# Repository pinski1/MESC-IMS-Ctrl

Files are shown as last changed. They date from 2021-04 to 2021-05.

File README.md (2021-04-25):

# MESC IMS Ctrl
A derivative of the Molony ESC. STM32F303 based BLDC logic board designed to interface to an IMS power stage.

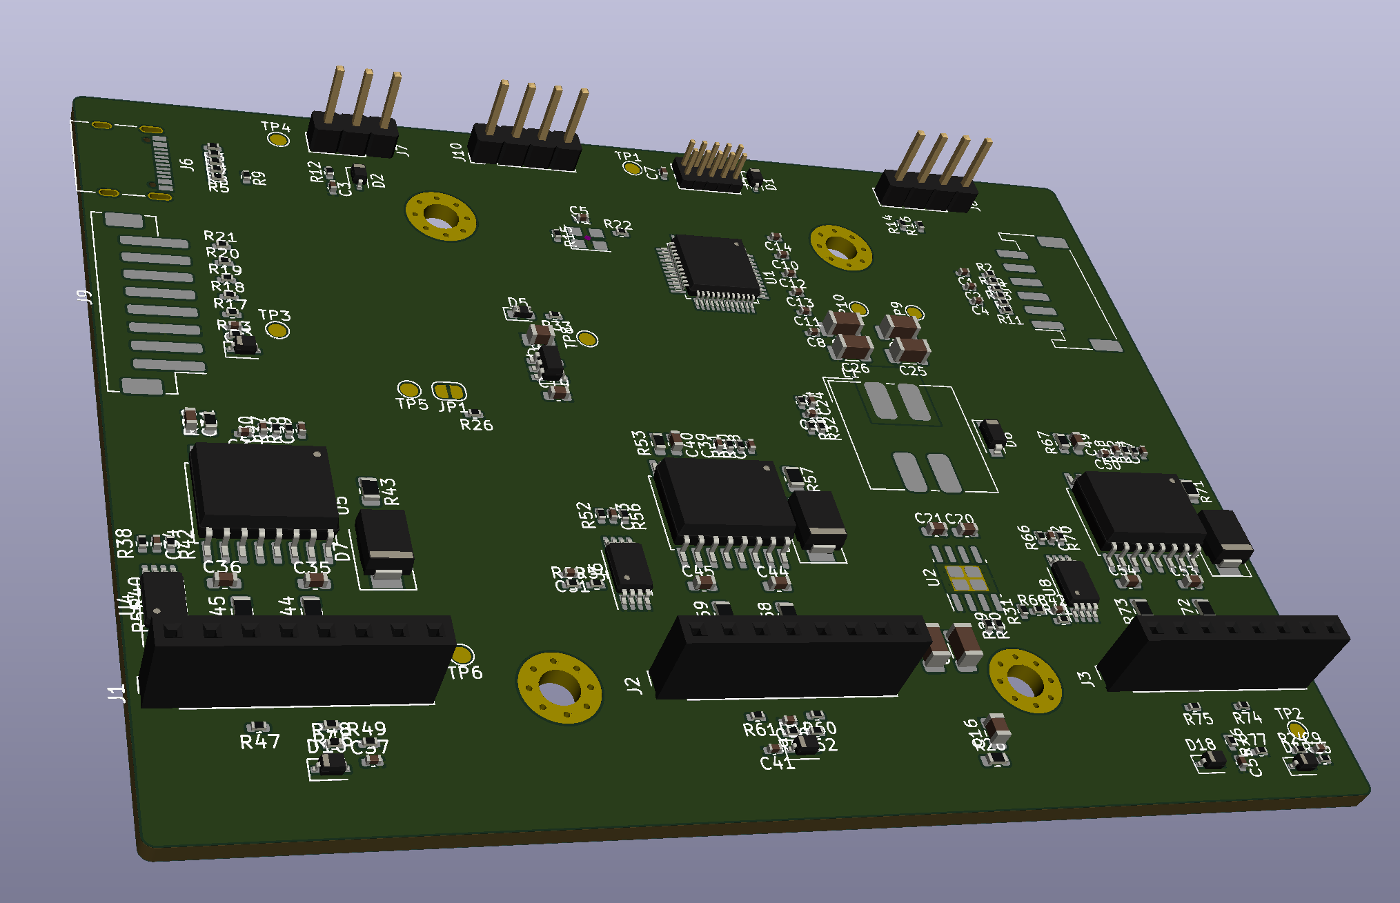
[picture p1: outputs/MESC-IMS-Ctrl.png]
An initial 3D render of the board.


Please see https://github.com/davidmolony/MESC_FOC_ESC for further details.

For the most recent schematic check out the 'outputs' folder.

This board is designed to fit on a 12FET power stage IMS PCB
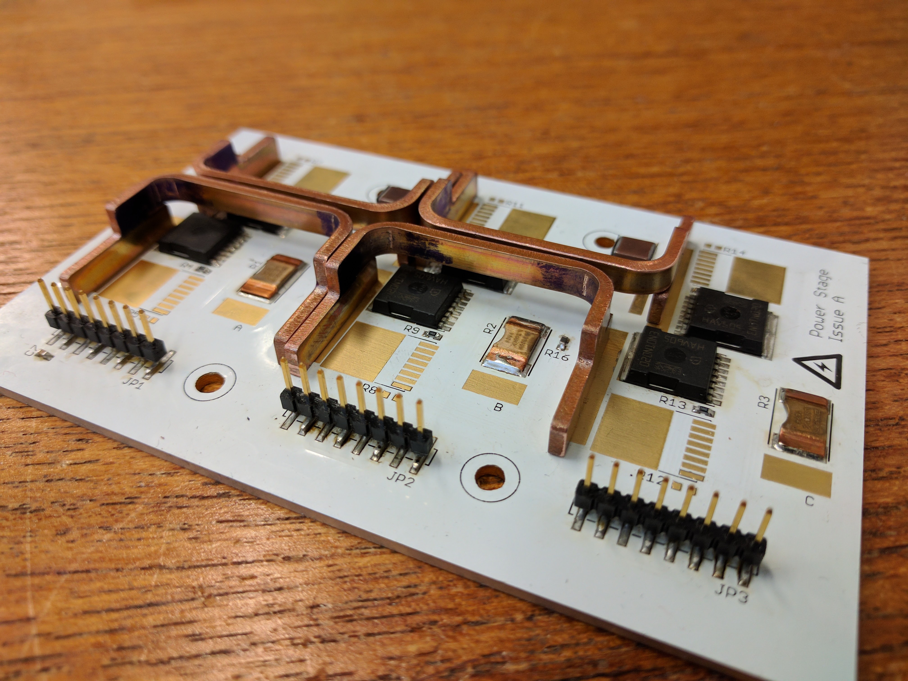
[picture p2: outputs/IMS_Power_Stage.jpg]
The 12FET Power stage with only half the MOSFETs


## "MESC_IMS_Ctrl.sch"

* Using STM32F303 like MESC_FOC_ESC
* Using USB 2.0 type C connector for future compatibility
* Using VESC-style connectors for control & hall effect sensors
* Has facility to monitor a thermistor mounted to the power stage PCB
* Can monitor the battery voltage
* Can be powered via USB for configuration on the desk

## "psu.sch"
This sheet contains the power supplies for the ESC. It's designed to accept +40-50V input but won't activate at voltages less than +25V. The LM5-017 is a popular and robust SMPS buck convertor. To minimise supply rail noise but supply the requisite ripple for the feedback circuitry the Texas Instruments application note here: https://www.ti.com/lit/an/snva166a/snva166a.pdf was consulted.

By using a coupled inductor it is possible to get a 2nd, unregulated, output that can be 'stacked' on top of the regulated output. This provides a ~10V supply for the gate drivers. This method of using a coupled inductor to generate a 2nd output is detailed in this Texas Instruments application note here: https://www.ti.com/lit/pdf/snva674.

The +3V3 rail for the microcontroller and current amplifiers comes from a standard SOT23-5 LDO. This minimises noise artefacts and is a simple, low cost, low complexity way of generating this rail.

## "phase.sch"
As this board will plug into the separate power stage PCB it was decided to use isolated gate driver chips. As the gate signals are treated as differential signals this should hopefully allow for fast control while minimising noise, minimising ripple and self-turn-on. The UCC21520 is another well regarded chip. 

The INA240 is used for high speed current sensing, it will take the differential phase current sense signals at the phase voltage and convert them to a single ended current signal with 0A being around 1.65V. There is no additional filtering as this will affect the response of the current amplifier.

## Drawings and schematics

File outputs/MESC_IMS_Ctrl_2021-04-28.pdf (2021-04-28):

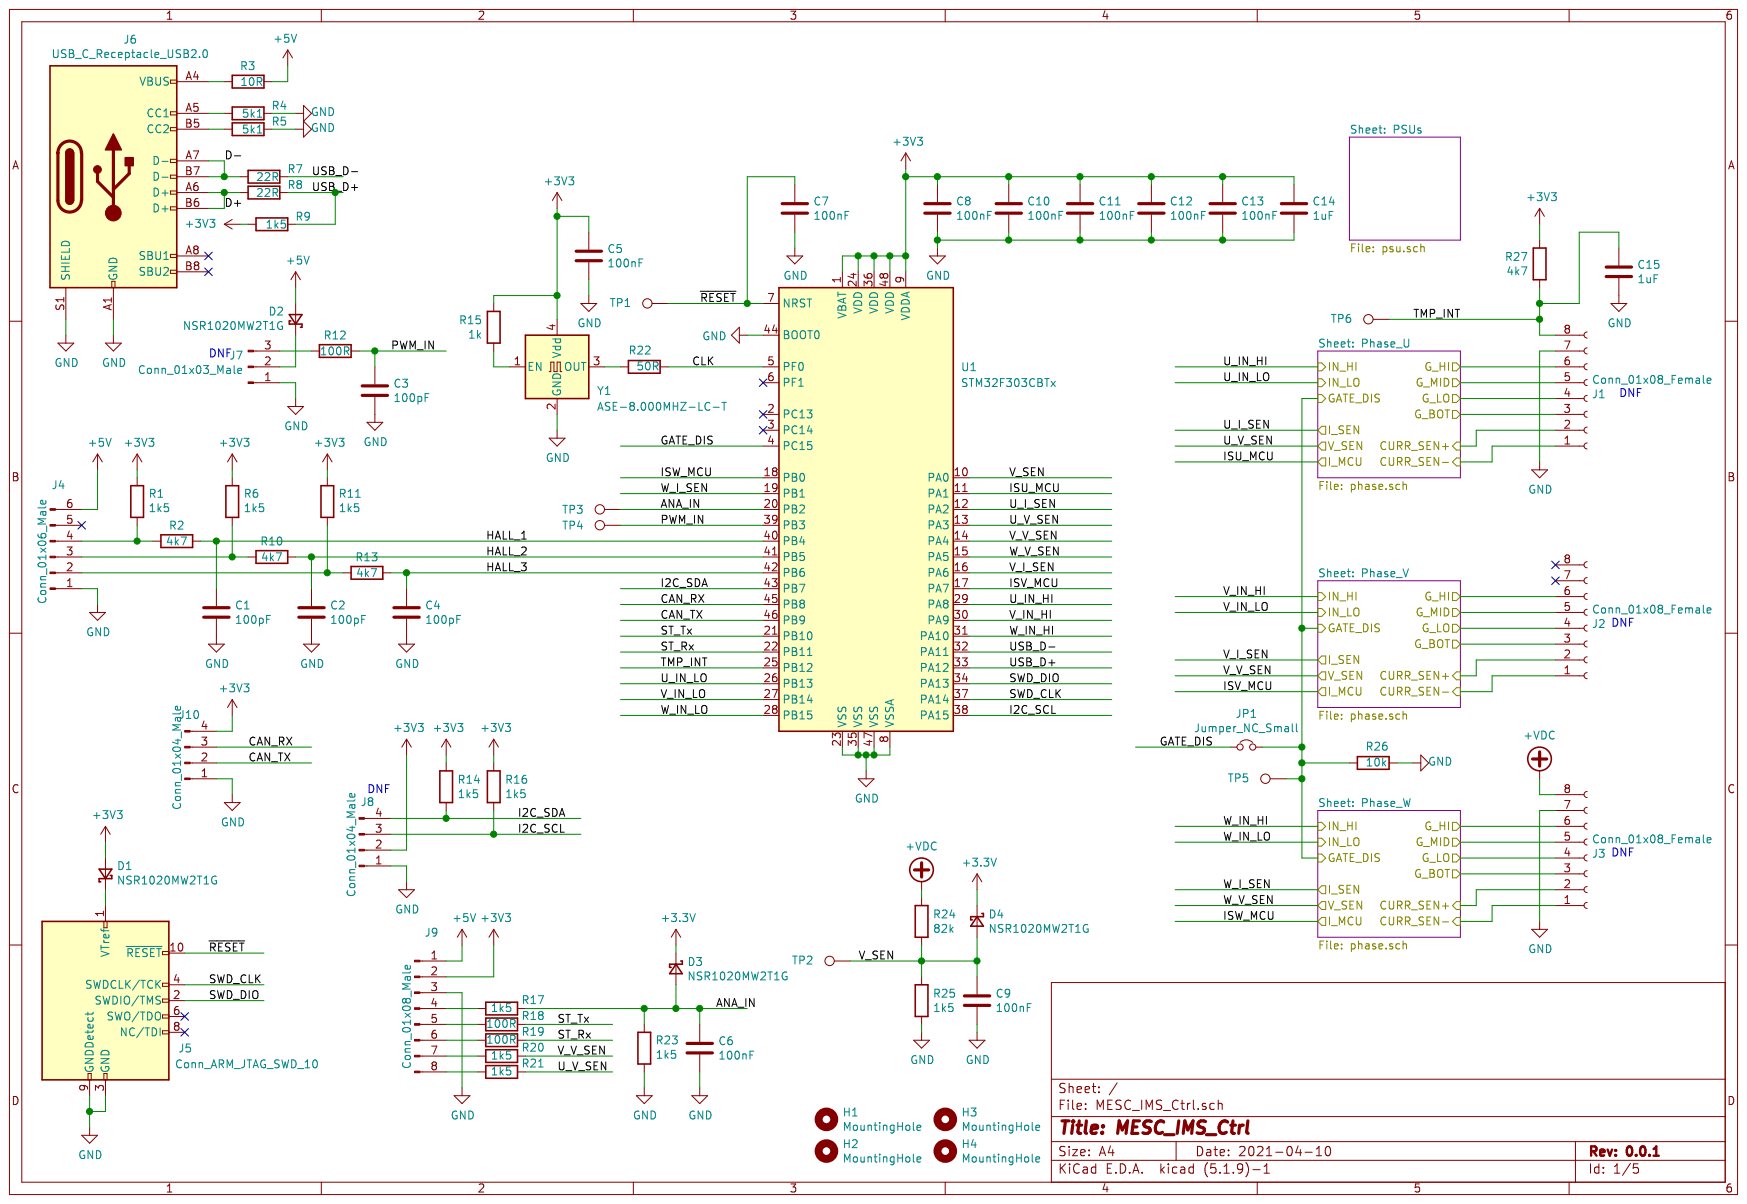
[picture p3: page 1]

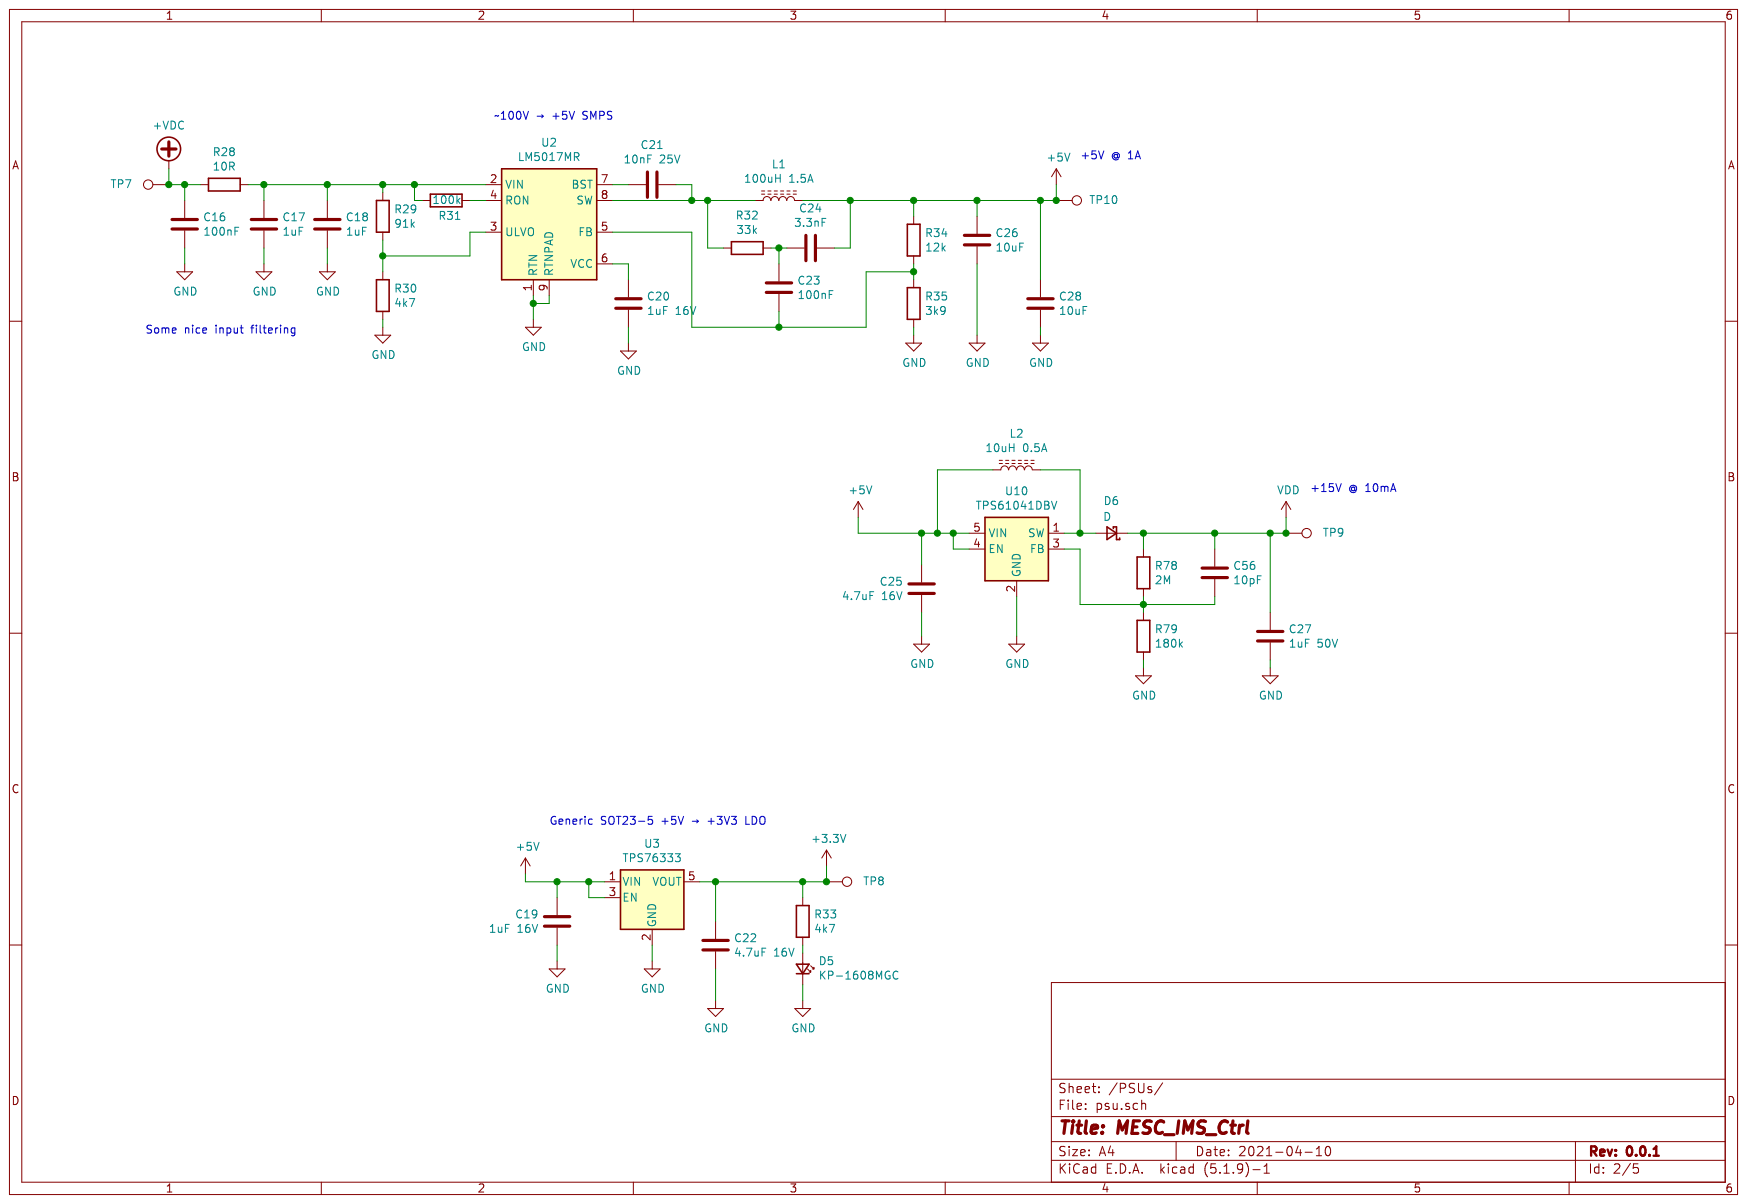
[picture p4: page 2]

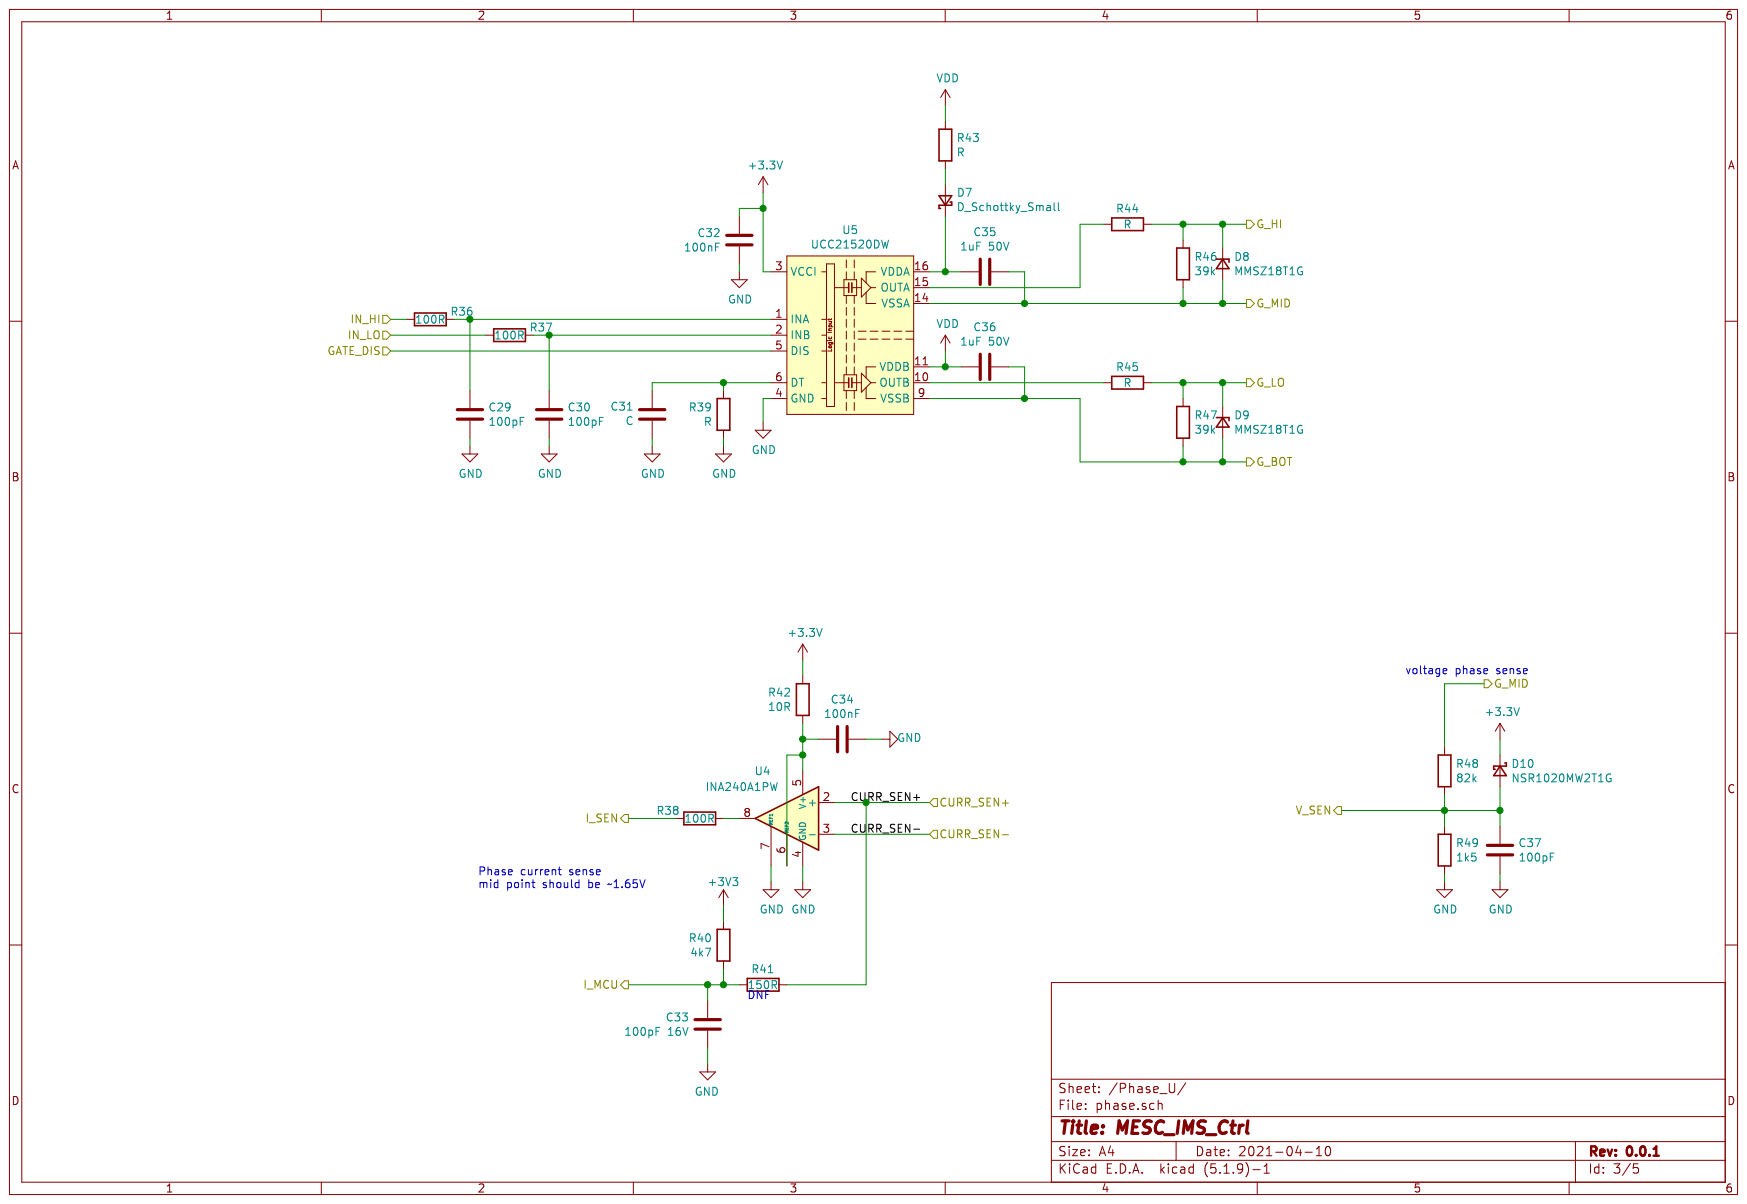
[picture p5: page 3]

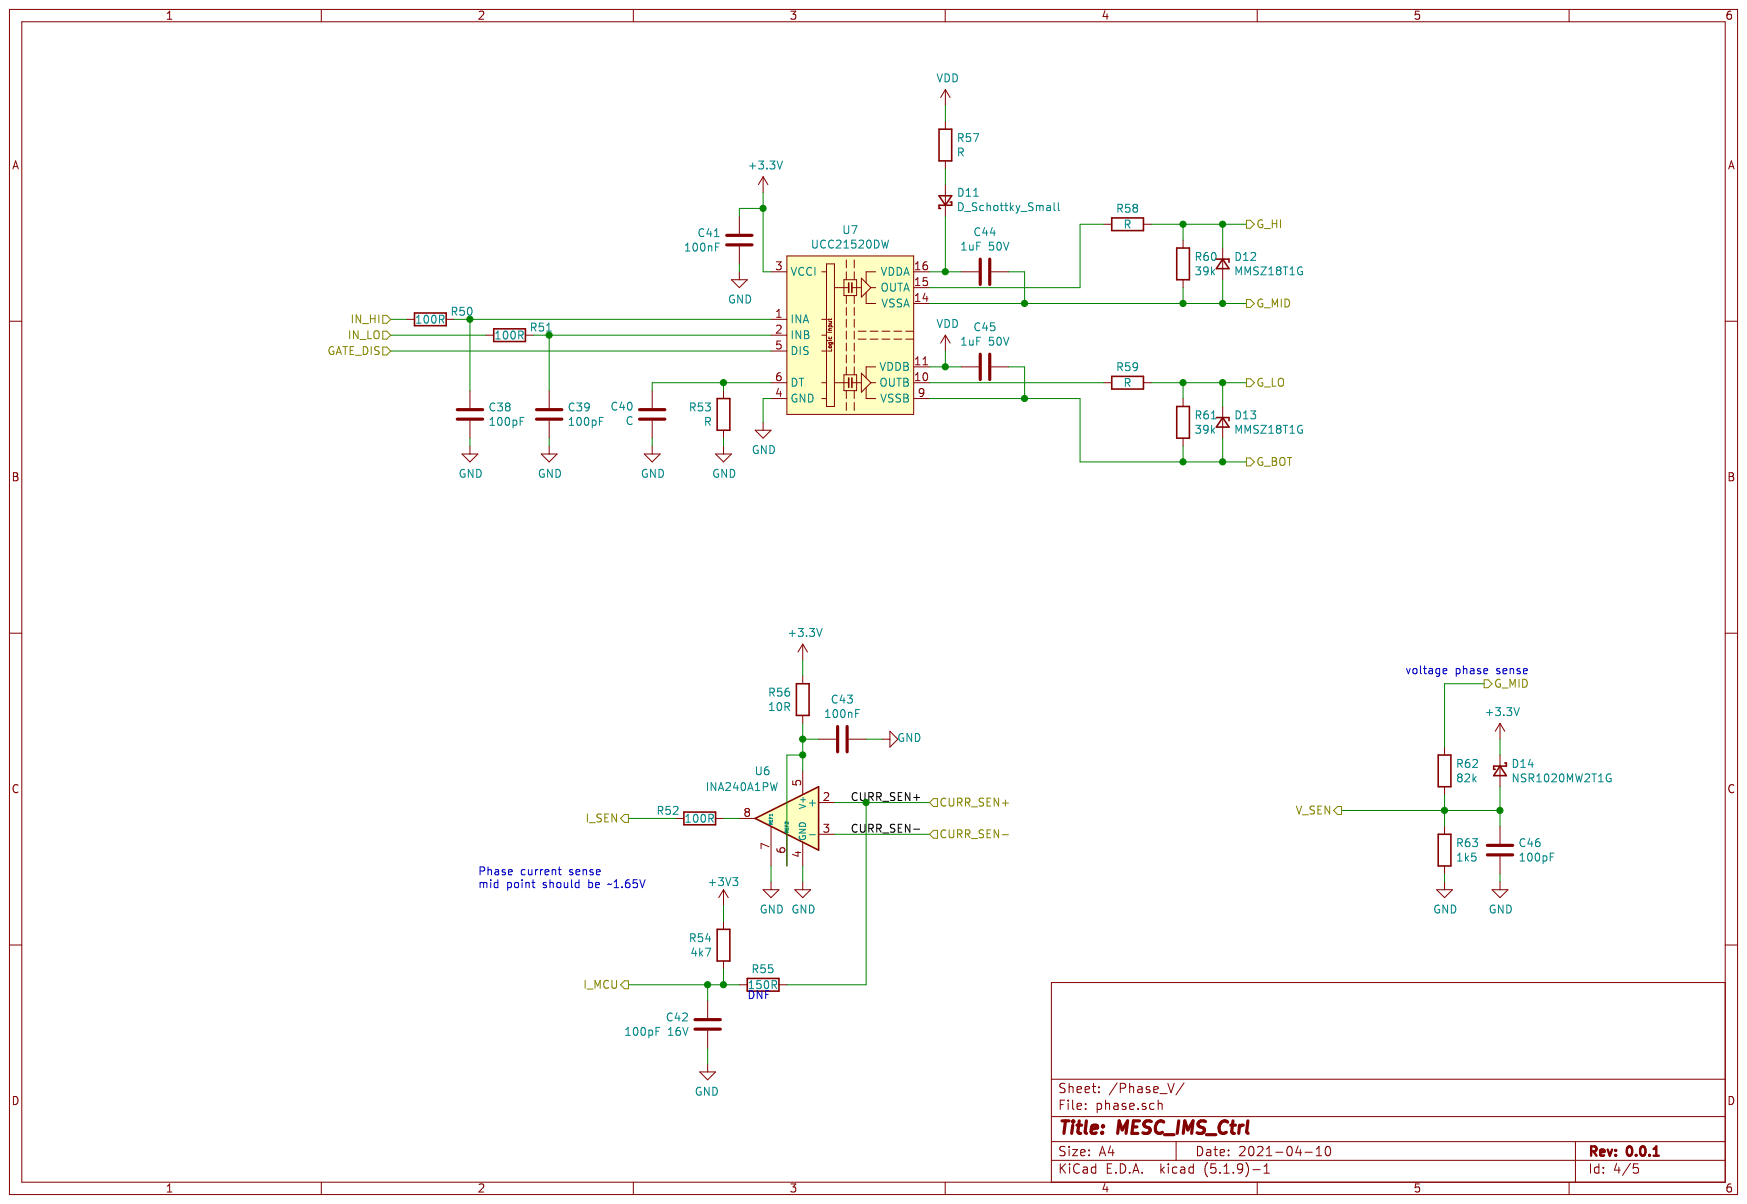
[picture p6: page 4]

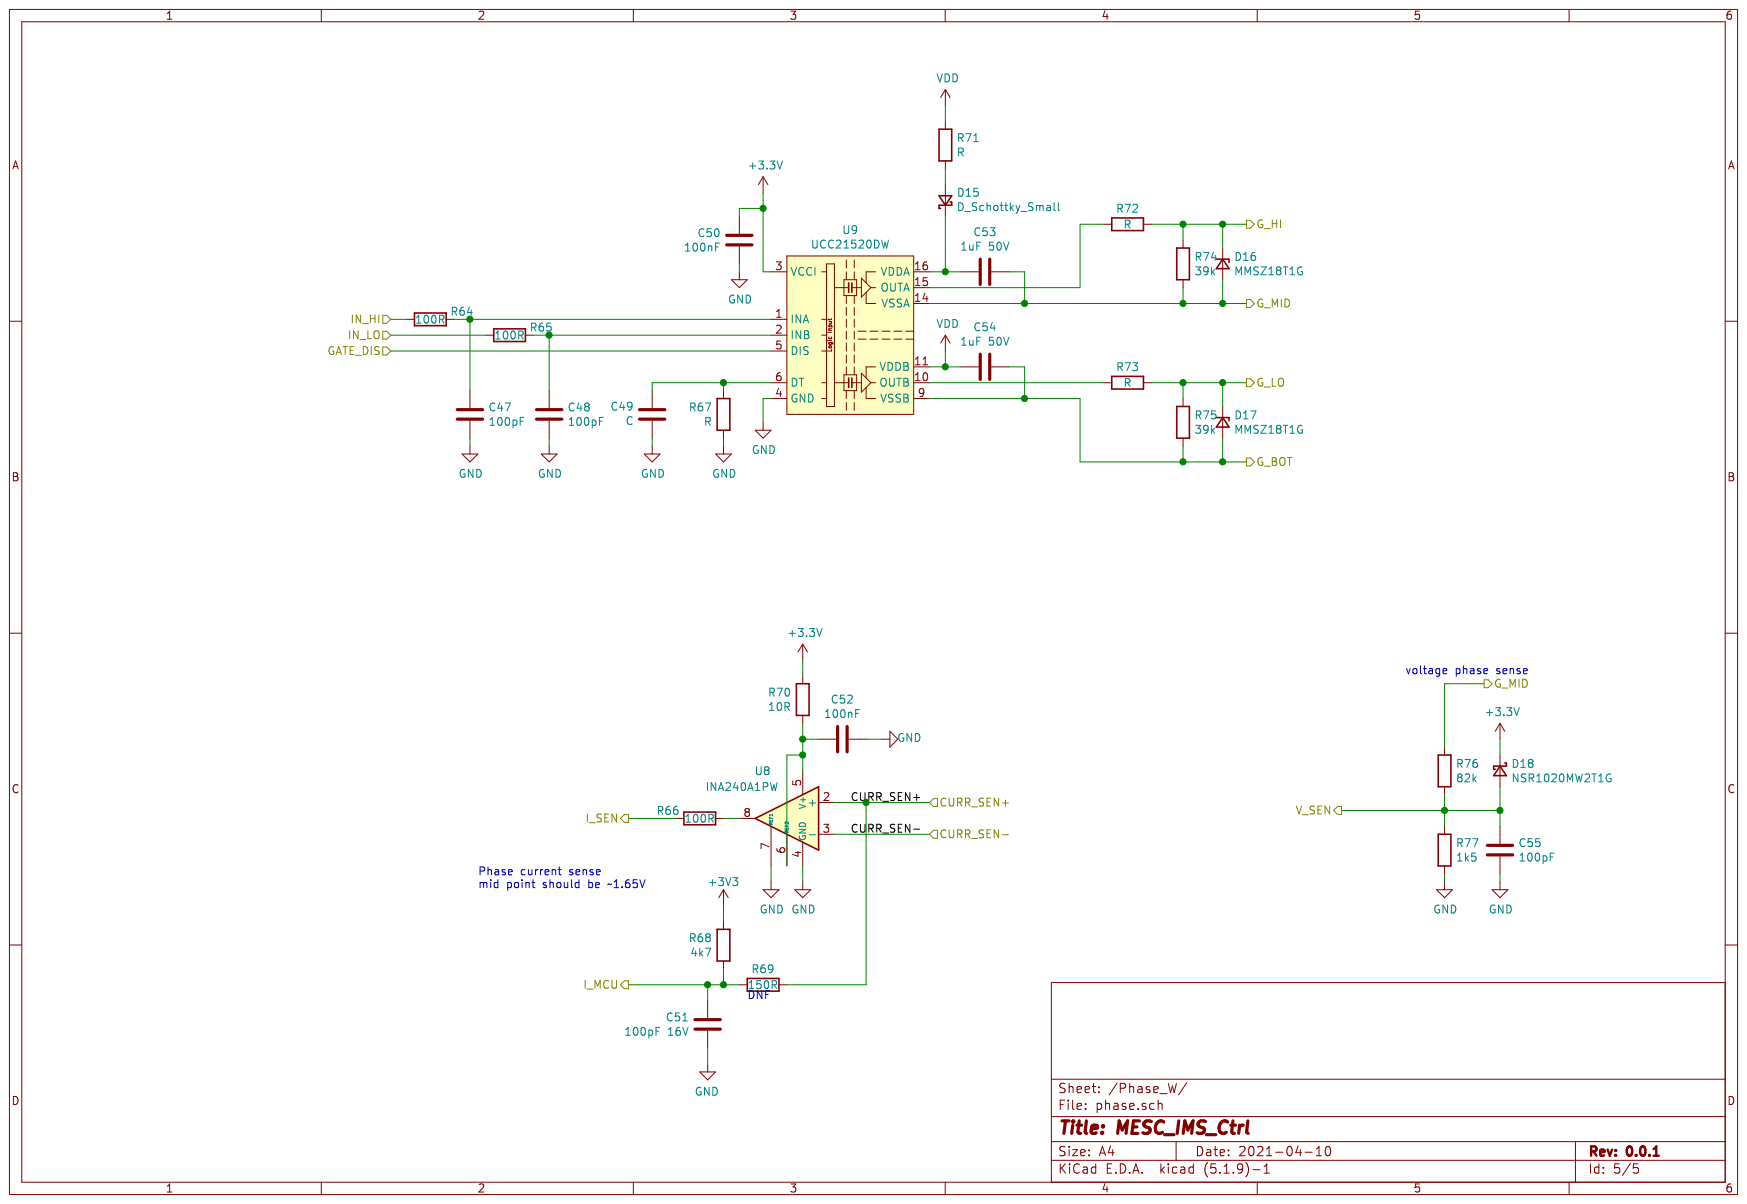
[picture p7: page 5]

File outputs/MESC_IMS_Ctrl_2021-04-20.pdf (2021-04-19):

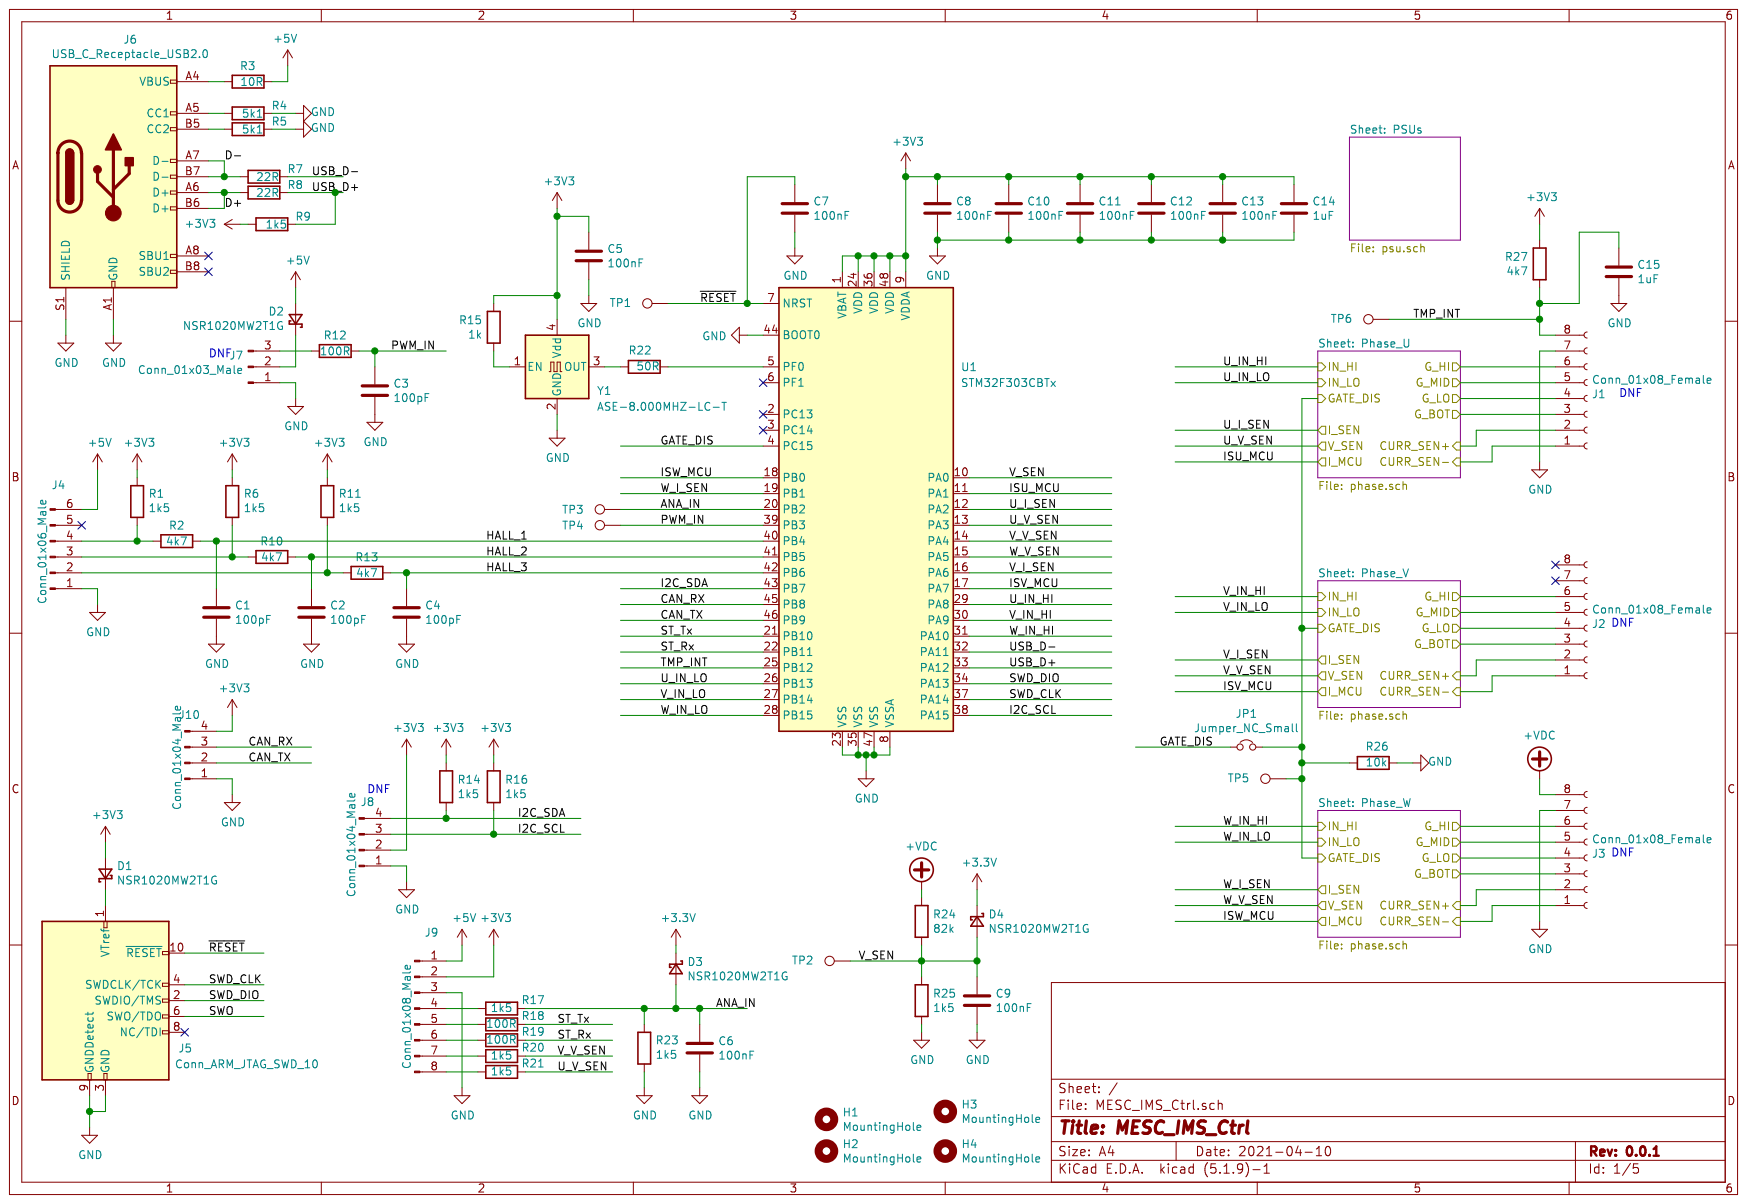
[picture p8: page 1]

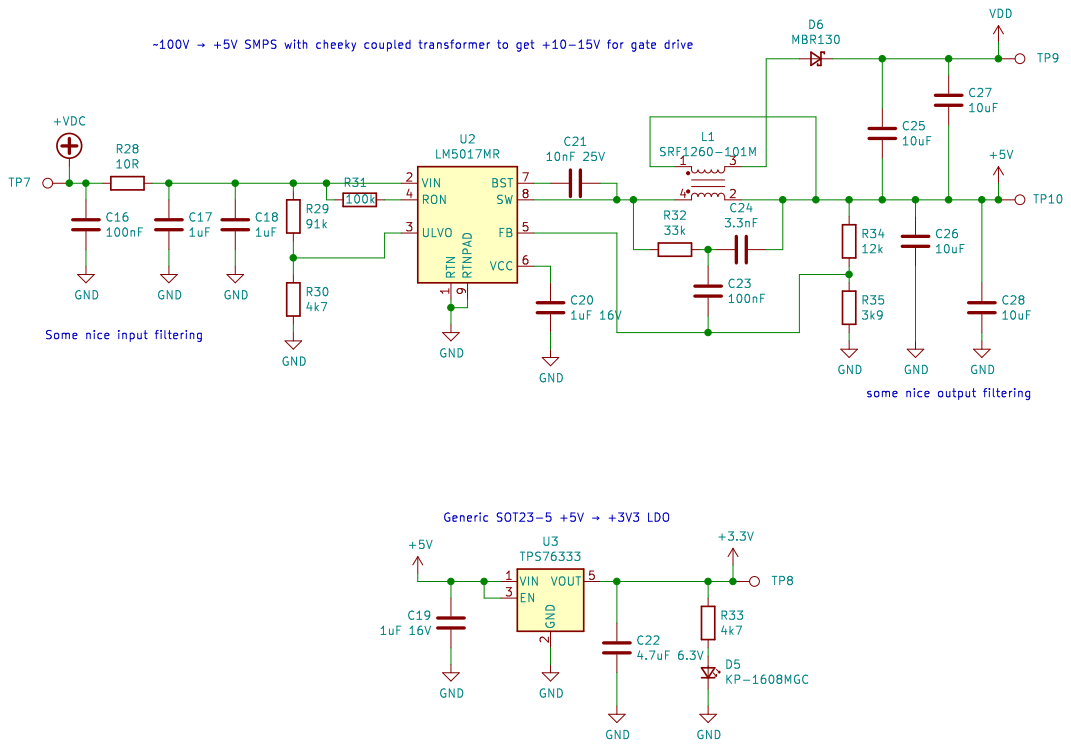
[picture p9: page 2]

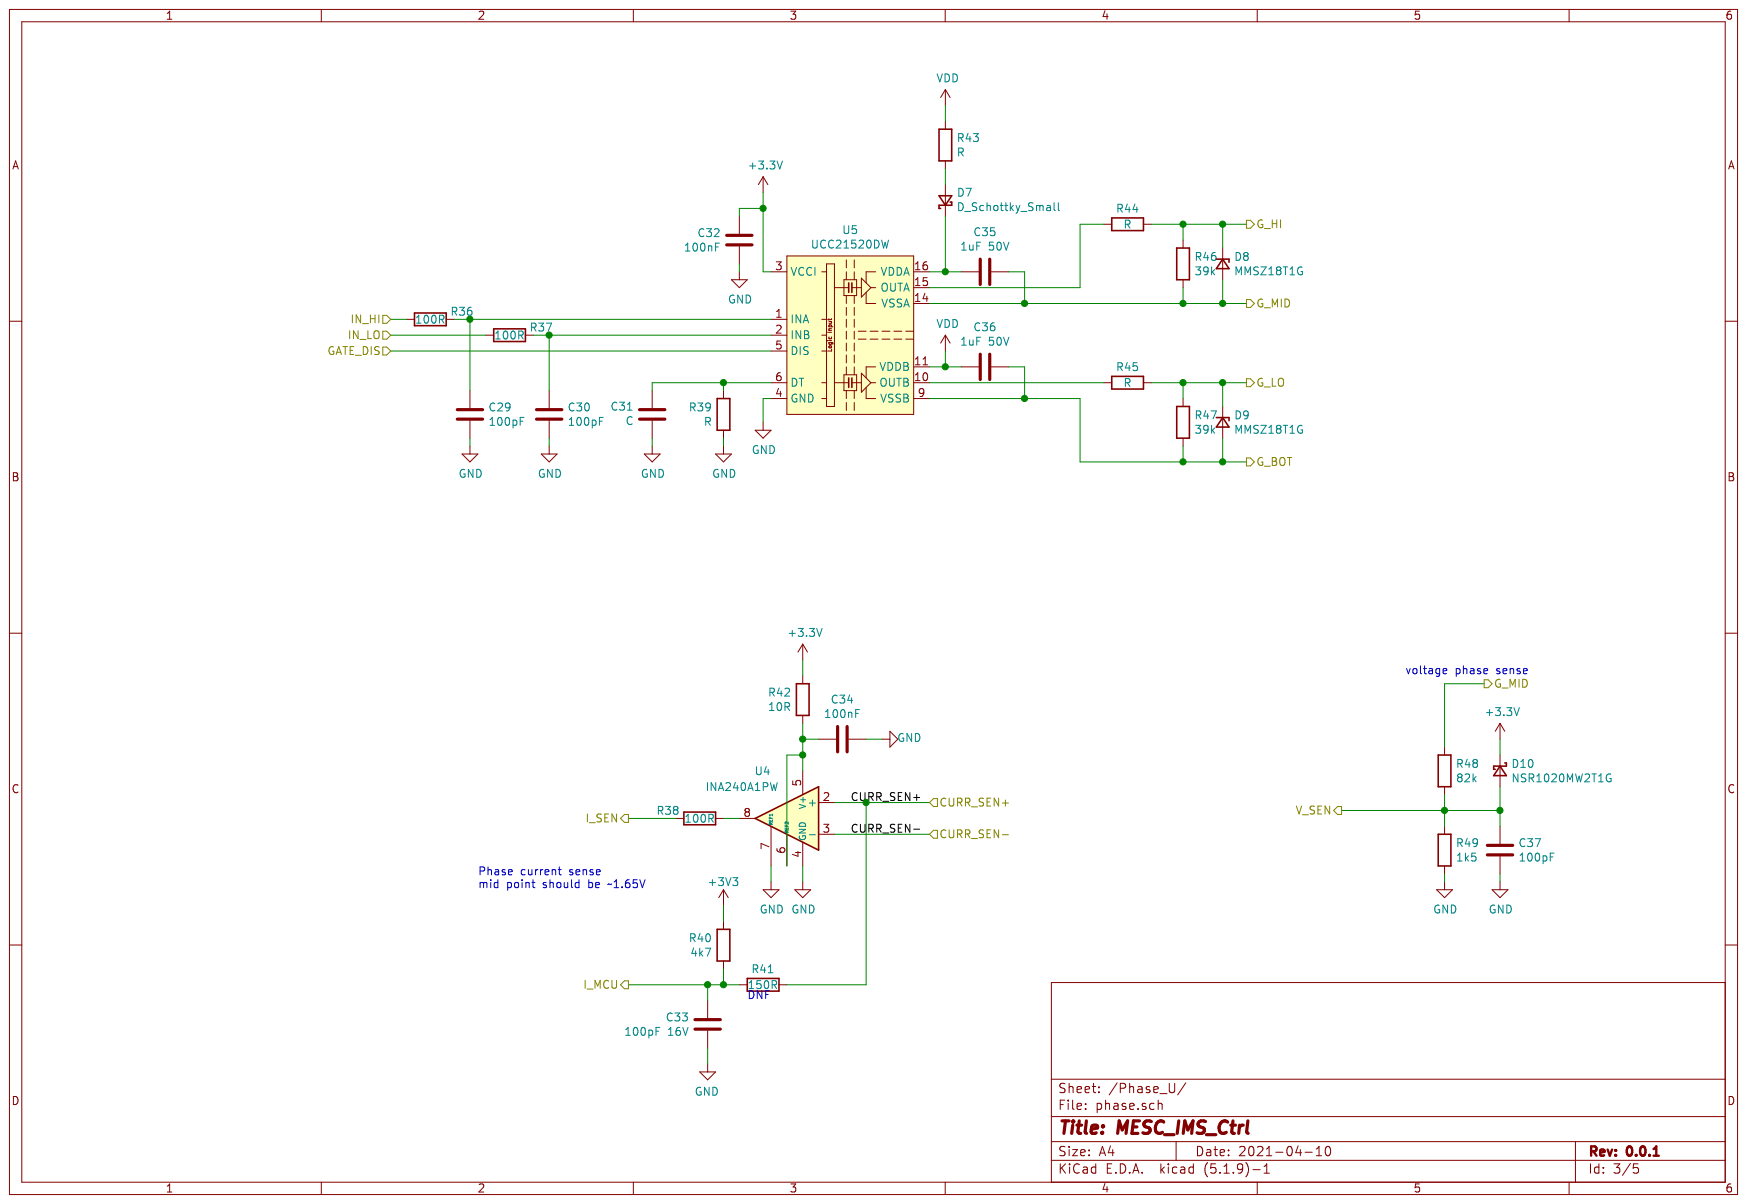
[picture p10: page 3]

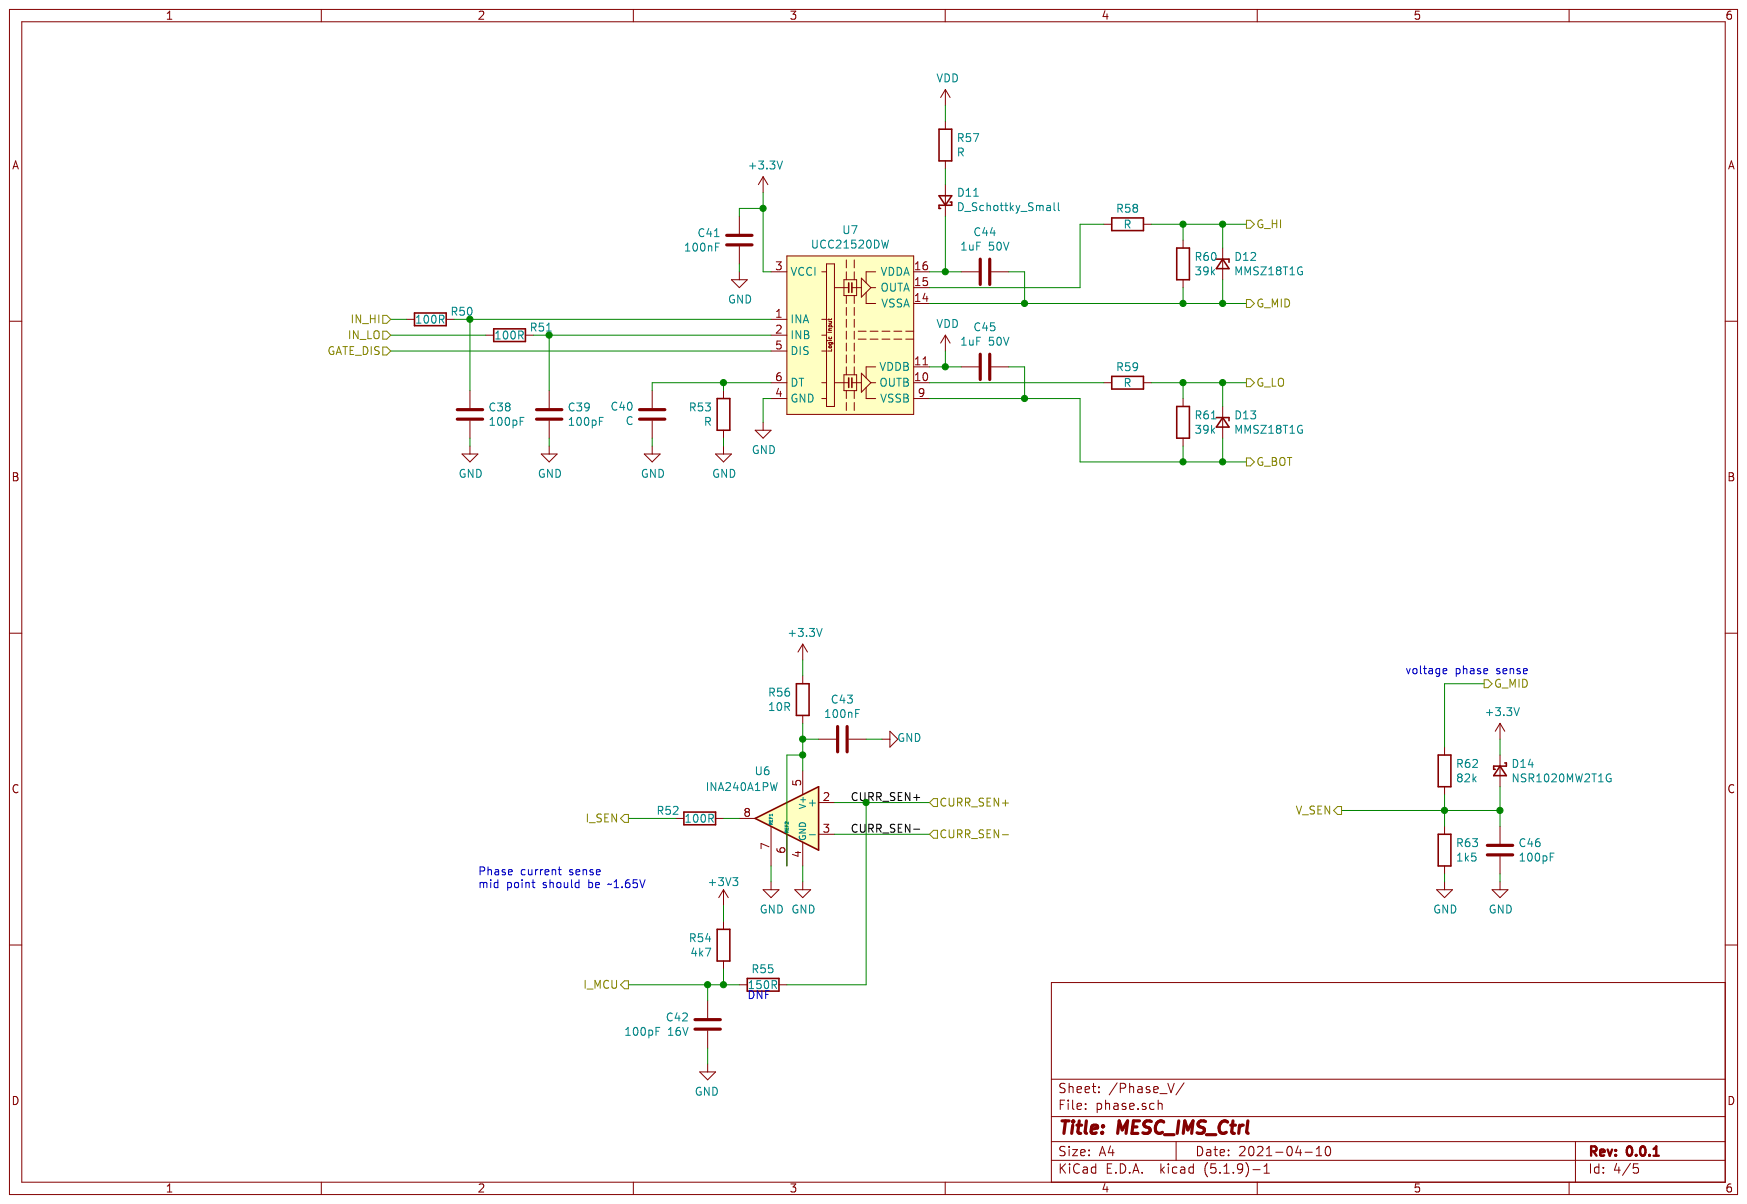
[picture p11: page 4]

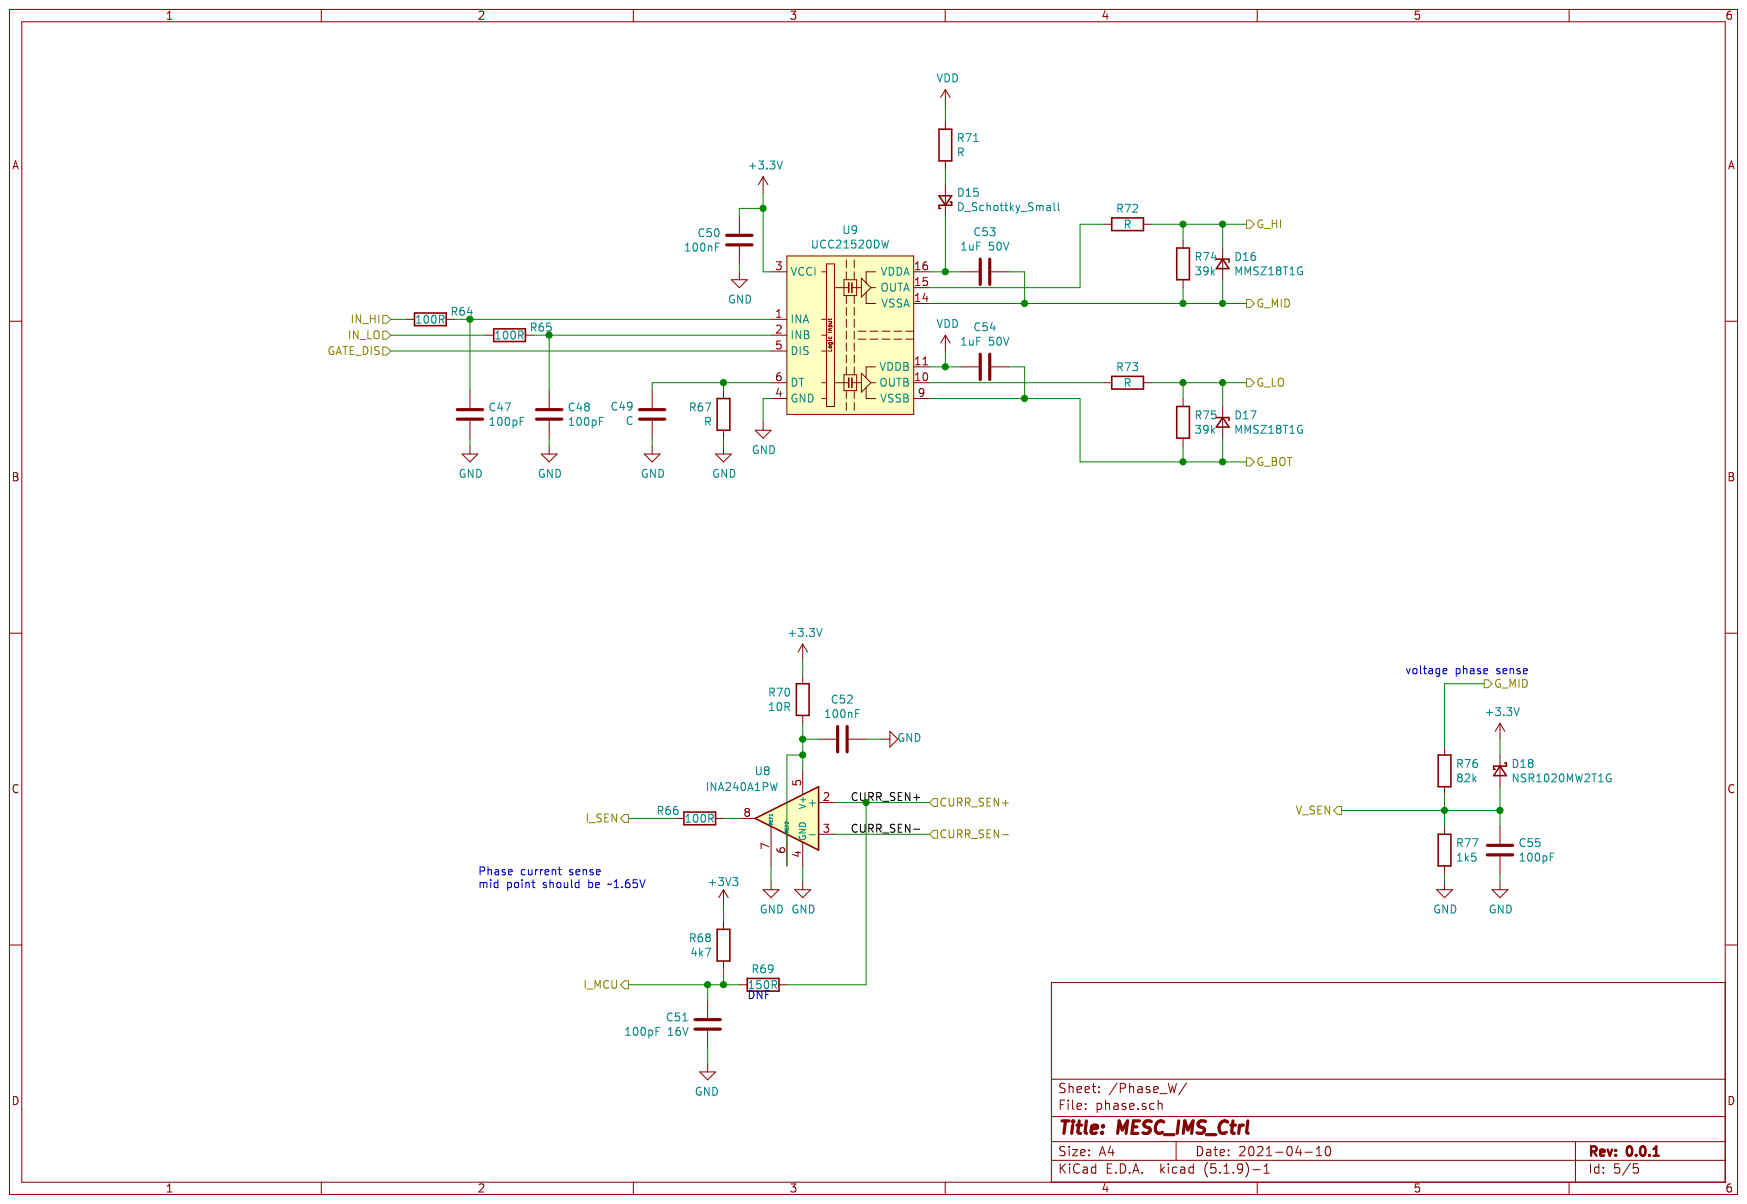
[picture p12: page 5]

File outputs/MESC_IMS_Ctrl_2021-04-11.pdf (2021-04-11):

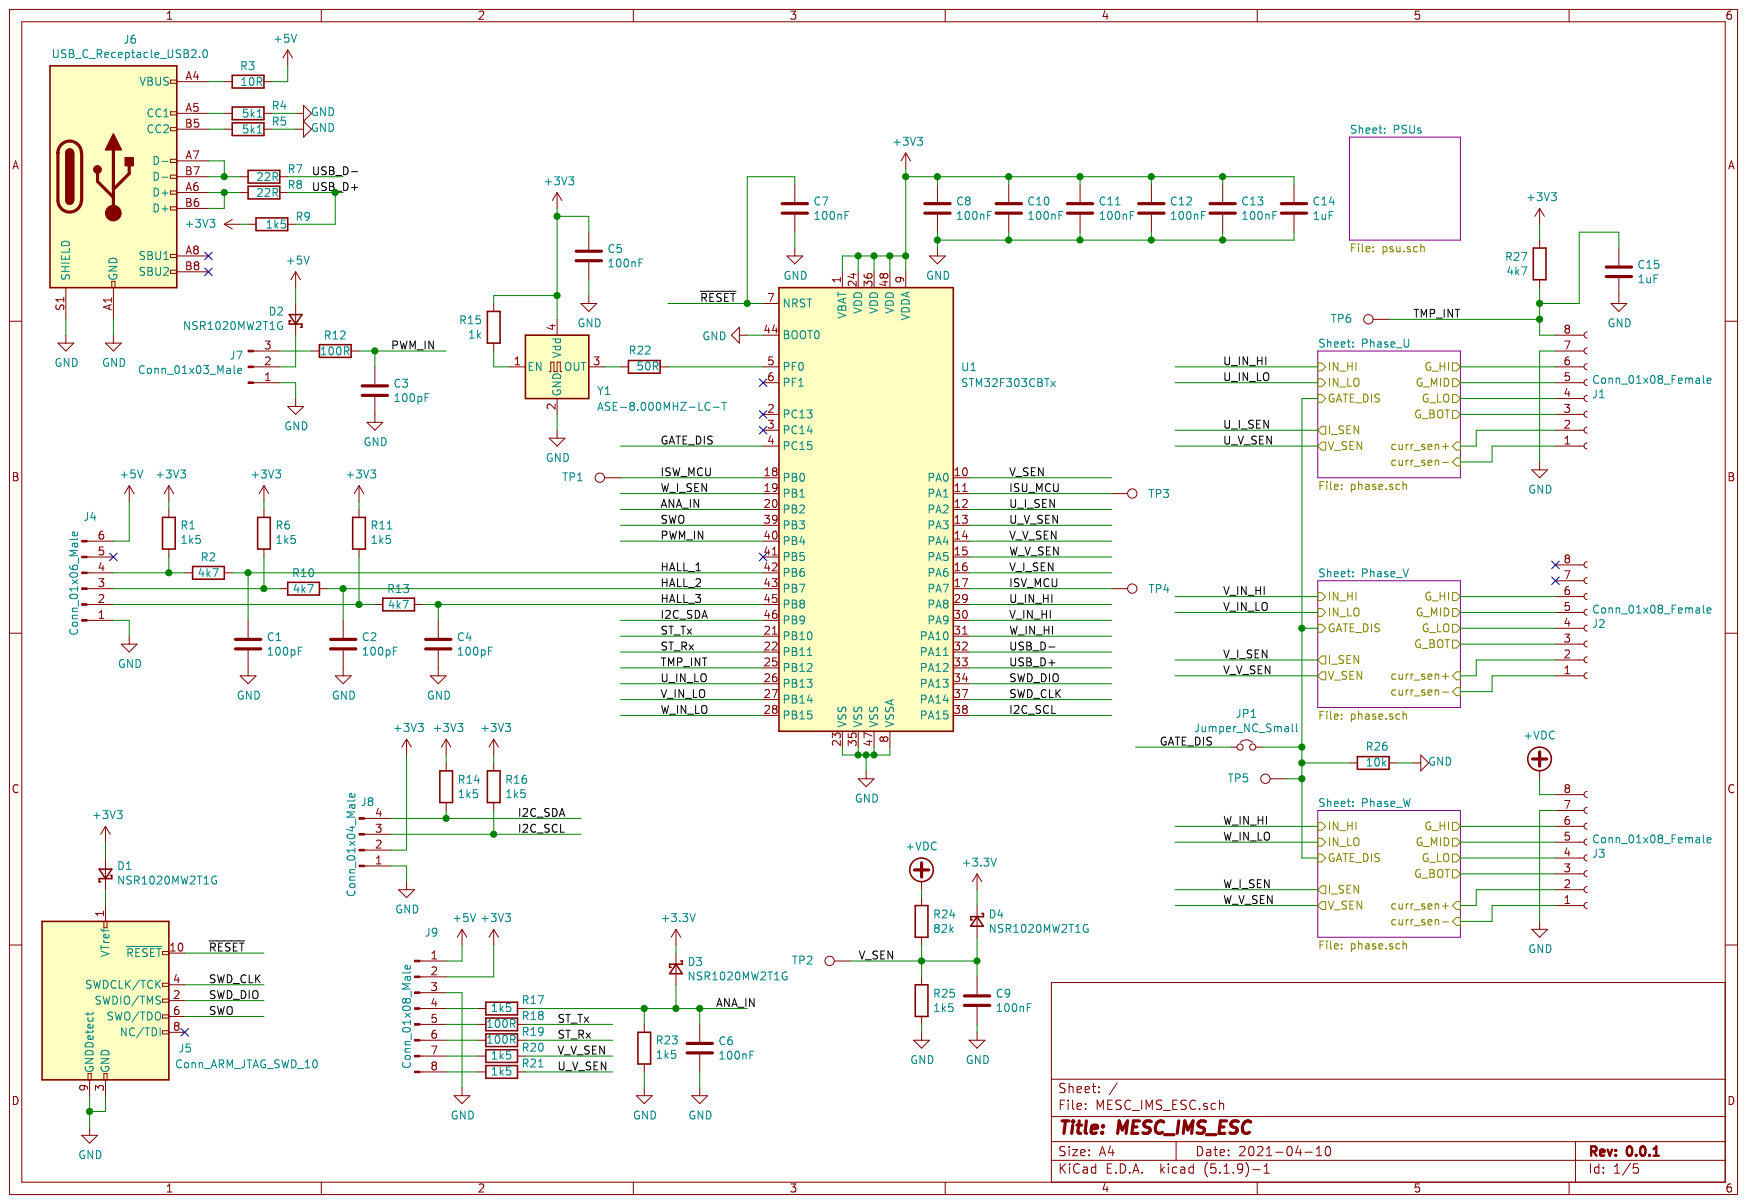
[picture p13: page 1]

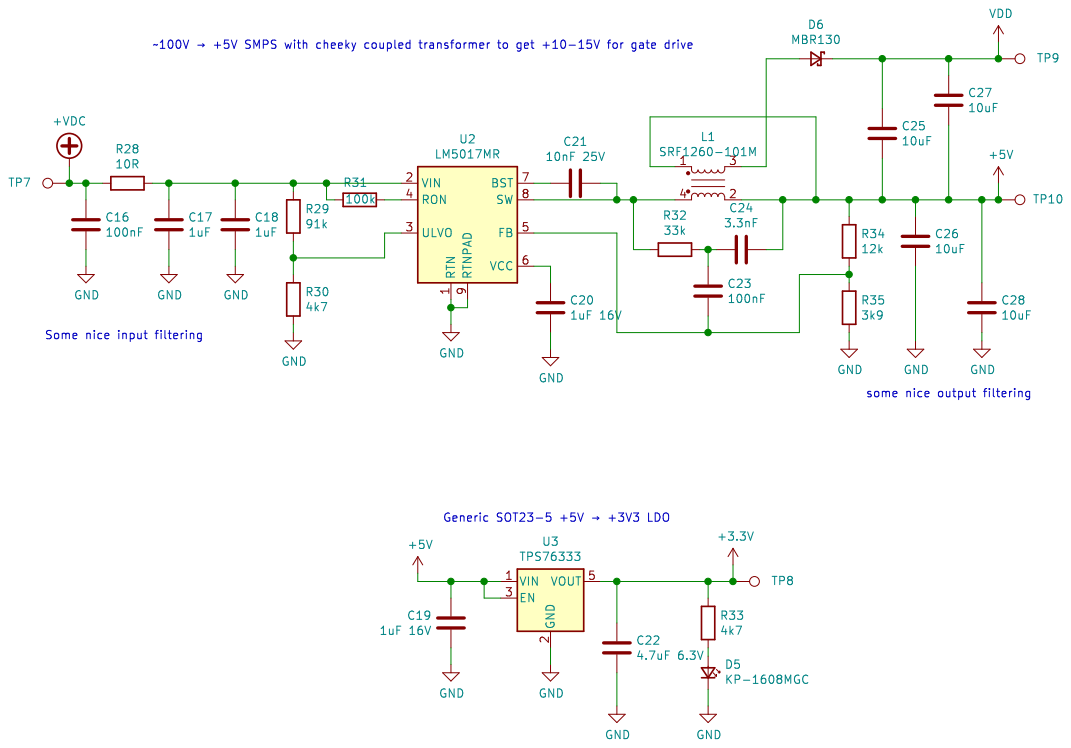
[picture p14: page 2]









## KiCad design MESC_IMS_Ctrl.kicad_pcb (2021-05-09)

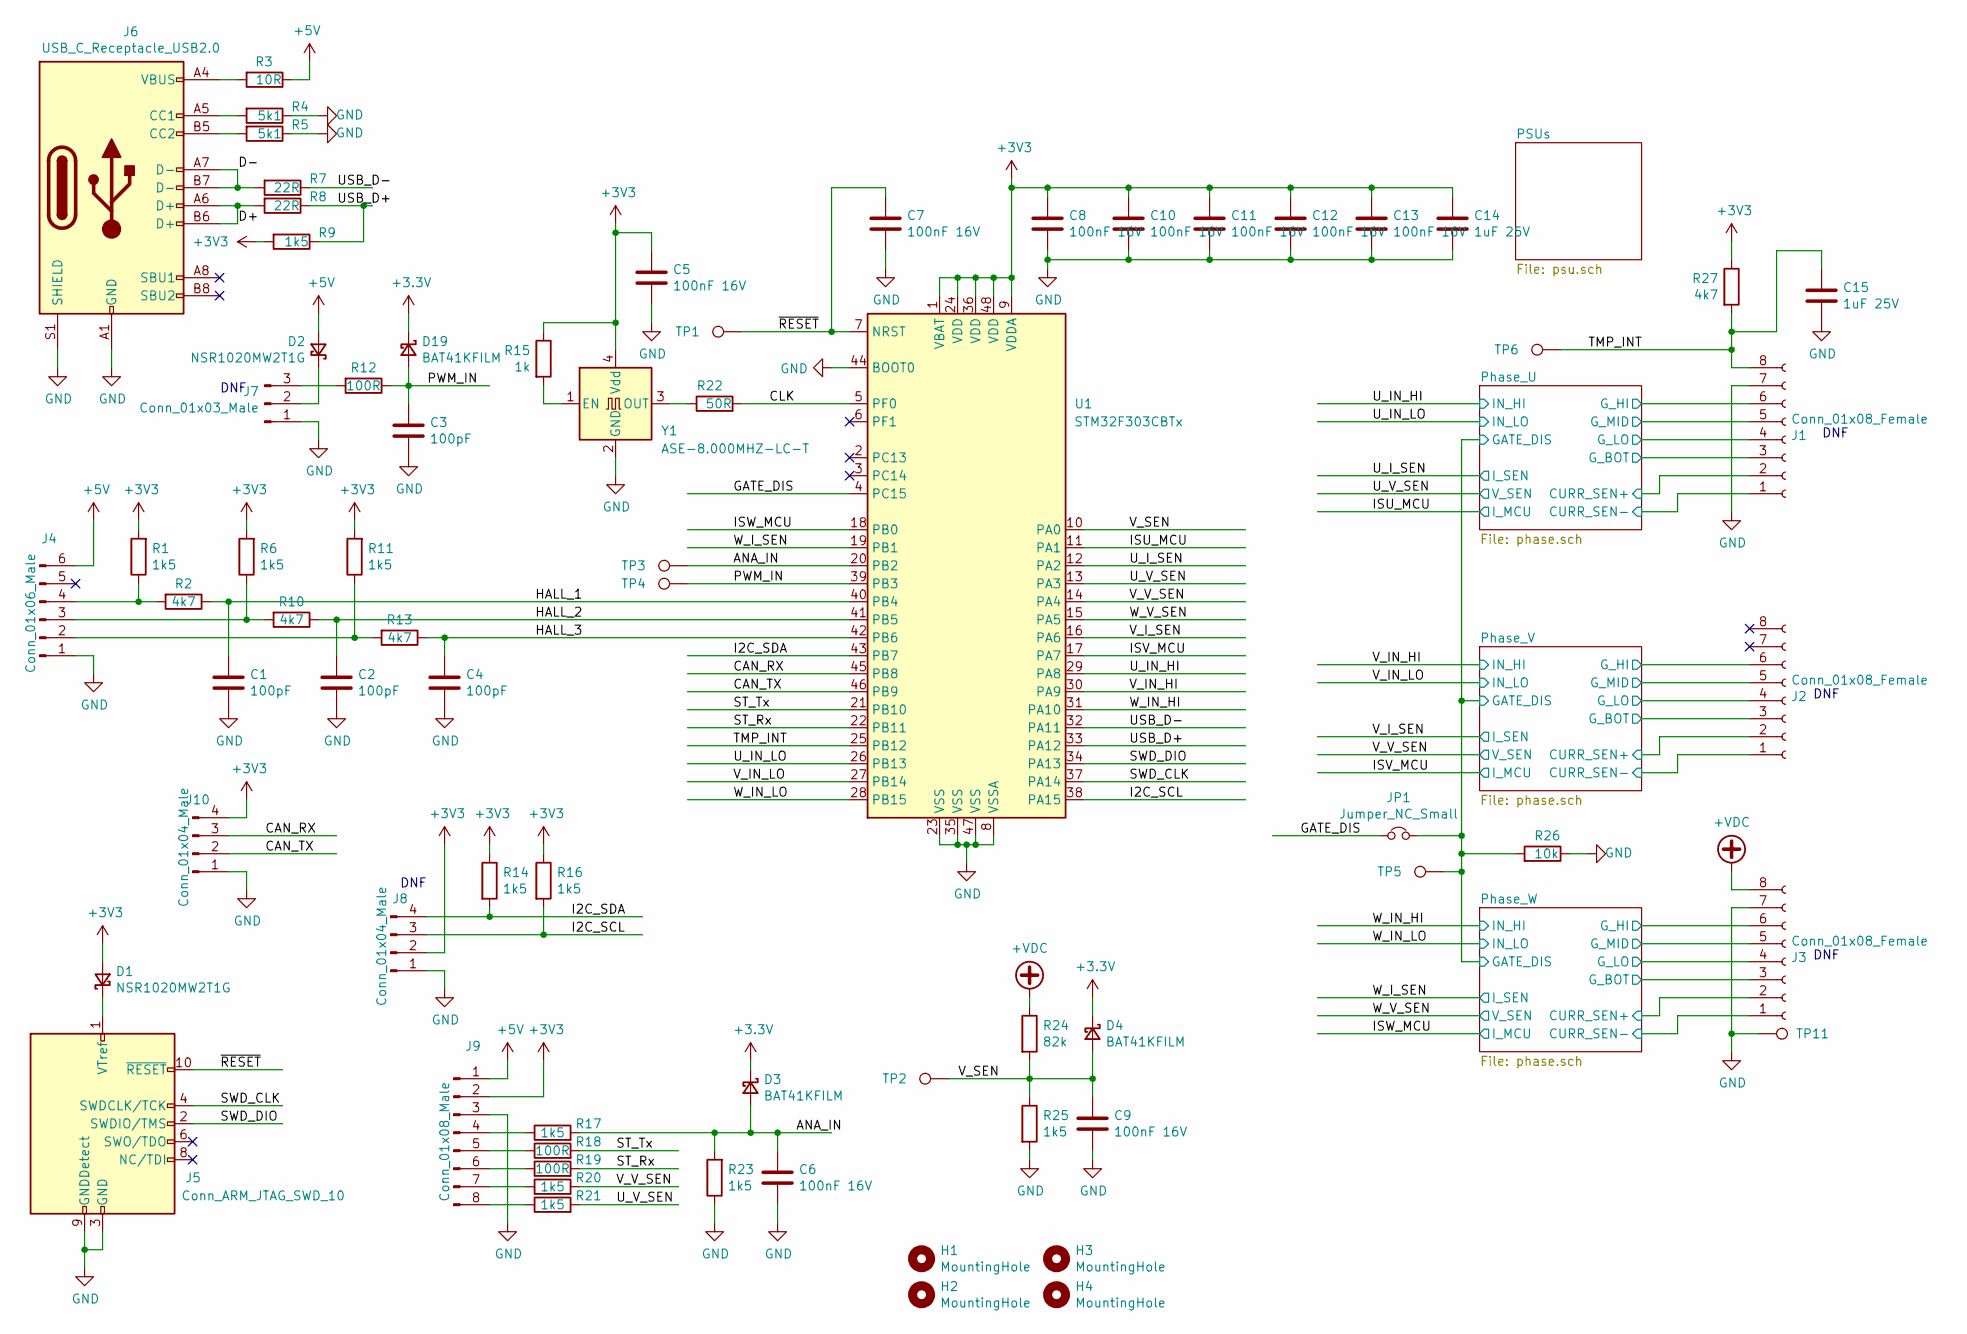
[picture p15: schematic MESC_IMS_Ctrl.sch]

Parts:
C1, C2, C3, C4: 100pF; C_0402_1005Metric; LCSC C1546
C5, C6, C7, C8, C9, C10, C11, C12, C13: 100nF 16V; C_0402_1005Metric; LCSC C1525
C14, C15: 1uF 25V; C_0402_1005Metric; LCSC C52923
D1, D2: NSR1020MW2T1G; D_SOD-323; LCSC C116953
D3, D4, D19: BAT41KFILM; D_SOD-523; LCSC C73150
H1, H2, H3, H4: MountingHole; MountingHole_3.2mm_M3_Pad_Via
J1, J2, J3: Conn_01x08_Female; PinSocket_1x08_P2.54mm_Vertical
J4: Conn_01x06_Male; JST_PH_S6B-PH-SM4-TB_1x06-1MP_P2.00mm_Horizontal; LCSC C225237
J5: Conn_ARM_JTAG_SWD_10; PinHeader_2x05_P1.27mm_Vertical; LCSC C239059
J6: USB_C_Receptacle_USB2.0; USB_C_Receptacle_Palconn_UTC16-G; LCSC C165948
J7: Conn_01x03_Male; PinHeader_1x03_P2.54mm_Vertical
J8, J10: Conn_01x04_Male; PinHeader_1x04_P2.54mm_Vertical
J9: Conn_01x08_Male; JST_PH_S8B-PH-SM4-TB_1x08-1MP_P2.00mm_Horizontal; LCSC C225239
JP1: Jumper_NC_Small; SolderJumper-2_P1.3mm_Bridged_RoundedPad1.0x1.5mm
R1, R6, R9, R11, R14, R16, R17, R20, R21, R23: 1k5; R_0402_1005Metric; LCSC C25867
R2, R10, R13, R27: 4k7; R_0402_1005Metric; LCSC C25900
R3: 10R; R_0402_1005Metric; LCSC C25077
R4, R5: 5k1; R_0402_1005Metric; LCSC C25905
R7, R8: 22R; R_0402_1005Metric; LCSC C25092
R12, R18, R19: 100R; R_0402_1005Metric; LCSC C25076
R15: 1k; R_0402_1005Metric; LCSC C11702
R22: 50R; R_0402_1005Metric; LCSC C25120
R24: 82k; R_0603_1608Metric; LCSC C23254
R25: 1k5; R_0603_1608Metric; LCSC C22843
R26: 10k; R_0402_1005Metric; LCSC C25744
TP1, TP2, TP3, TP4, TP5, TP6, TP11: TestPoint; TestPoint_Pad_D1.0mm
U1: STM32F303CBTx; LQFP-48_7x7mm_P0.5mm; LCSC C108516
Y1: ASE-8.000MHZ-LC-T; Oscillator_SMD_Abracon_ASE-4Pin_3.2x2.5mm; LCSC C295522

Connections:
+5V: D2.2 (A), J4.6, J9.1, R3.1; also elsewhere on the board
+VDC: J3.8, R24.1; also elsewhere on the board
/ANA_IN: C6.1, D3.2 (A), R17.2, R23.2, TP3.1, U1.20 (PB2)
/CAN_RX: J10.3, U1.45 (PB8)
/CAN_TX: J10.2, U1.46 (PB9)
/CLK: R22.2, U1.5 (PF0)
/D+: J6.A6 (D+), J6.B6 (D+), R8.2
/D-: J6.A7 (D-), J6.B7 (D-), R7.2
/GATE_DIS: JP1.1, U1.4 (PC15)
/HALL_1: C1.1, R2.1, U1.40 (PB4)
/HALL_2: C2.1, R10.1, U1.41 (PB5)
/HALL_3: C4.1, R13.1, U1.42 (PB6)
/I2C_SCL: J8.3, R16.2, U1.38 (PA15)
/I2C_SDA: J8.4, R14.2, U1.43 (PB7)
/ISU_MCU: U1.11 (PA1); also elsewhere on the board
/ISV_MCU: U1.17 (PA7); also elsewhere on the board
/ISW_MCU: U1.18 (PB0); also elsewhere on the board
/PWM_IN: C3.1, D19.2 (A), R12.1, TP4.1, U1.39 (PB3)
/Phase_U/CURR_SEN+: J1.2; also elsewhere on the board
/Phase_U/CURR_SEN-: J1.1; also elsewhere on the board
/Phase_U/GATE_DIS: JP1.2, R26.2, TP5.1; also elsewhere on the board
/Phase_U/G_BOT: J1.3; also elsewhere on the board
/Phase_U/G_HI: J1.6; also elsewhere on the board
/Phase_U/G_LO: J1.4; also elsewhere on the board
/Phase_U/G_MID: J1.5; also elsewhere on the board
/Phase_V/CURR_SEN+: J2.2; also elsewhere on the board
/Phase_V/CURR_SEN-: J2.1; also elsewhere on the board
/Phase_V/G_BOT: J2.3; also elsewhere on the board
/Phase_V/G_HI: J2.6; also elsewhere on the board
/Phase_V/G_LO: J2.4; also elsewhere on the board
/Phase_V/G_MID: J2.5; also elsewhere on the board
/Phase_W/CURR_SEN+: J3.2; also elsewhere on the board
/Phase_W/CURR_SEN-: J3.1; also elsewhere on the board
/Phase_W/G_BOT: J3.3; also elsewhere on the board
/Phase_W/G_HI: J3.6; also elsewhere on the board
/Phase_W/G_LO: J3.4; also elsewhere on the board
/Phase_W/G_MID: J3.5; also elsewhere on the board
/ST_Rx: R19.2, U1.22 (PB11)
/ST_Tx: R18.2, U1.21 (PB10)
/SWD_CLK: J5.4 (SWDCLK/TCK), U1.37 (PA14)
/SWD_DIO: J5.2 (SWDIO/TMS), U1.34 (PA13)
/TMP_INT: C15.1, J1.8, R27.2, TP6.1, U1.25 (PB12)
/USB_D+: R8.1, R9.1, U1.33 (PA12)
/USB_D-: R7.1, U1.32 (PA11)
/U_IN_HI: U1.29 (PA8); also elsewhere on the board
/U_IN_LO: U1.26 (PB13); also elsewhere on the board
/U_I_SEN: U1.12 (PA2); also elsewhere on the board
/U_V_SEN: R21.2, U1.13 (PA3); also elsewhere on the board
/V_IN_HI: U1.30 (PA9); also elsewhere on the board
/V_IN_LO: U1.27 (PB14); also elsewhere on the board
/V_I_SEN: U1.16 (PA6); also elsewhere on the board
/V_SEN: C9.1, D4.2 (A), R24.2, R25.1, TP2.1, U1.10 (PA0)
/V_V_SEN: R20.2, U1.14 (PA4); also elsewhere on the board
/W_IN_HI: U1.31 (PA10); also elsewhere on the board
/W_IN_LO: U1.28 (PB15); also elsewhere on the board
/W_I_SEN: U1.19 (PB1); also elsewhere on the board
/W_V_SEN: U1.15 (PA5); also elsewhere on the board
/~RESET: C7.1, J5.10 (~RESET~), TP1.1, U1.7 (NRST)
GND: C1.2, C2.2, C3.2, C4.2, C5.2, C6.2, C7.2, C8.2, C9.2, C10.2, C11.2, C12.2, C13.2, C14.2, C15.2, J1.7, J3.7, J4.1, J5.3 (GND), J5.5 (GND), J5.9 (GNDDetect), J6.A1 (GND), J6.A12 (GND), J6.B1 (GND), J6.B12 (GND), J6.S1 (SHIELD), J7.1, J8.1, J9.3, J10.1, R4.1, R5.1, R23.1, R25.2, R26.1, TP11.1, U1.8 (VSSA), U1.23 (VSS), U1.35 (VSS), U1.44 (BOOT0), U1.47 (VSS), Y1.2 (GND); also elsewhere on the board
unnamed: D1.1 (K), J5.1 (VTref)
unnamed: D2.1 (K), J7.2
unnamed: J4.2, R11.1, R13.2
unnamed: J4.3, R6.1, R10.2
unnamed: J4.4, R1.1, R2.2
unnamed: J6.A4 (VBUS), J6.A9 (VBUS), J6.B4 (VBUS), J6.B9 (VBUS), R3.2
unnamed: J6.A5 (CC1), R4.2
unnamed: J6.B5 (CC2), R5.2
unnamed: J7.3, R12.2
unnamed: J9.4, R17.1
unnamed: J9.5, R18.1
unnamed: J9.6, R19.1
unnamed: J9.7, R20.1
unnamed: J9.8, R21.1
unnamed: R15.2, Y1.1 (EN)
unnamed: R22.1, Y1.3 (OUT)

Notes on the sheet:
DNF

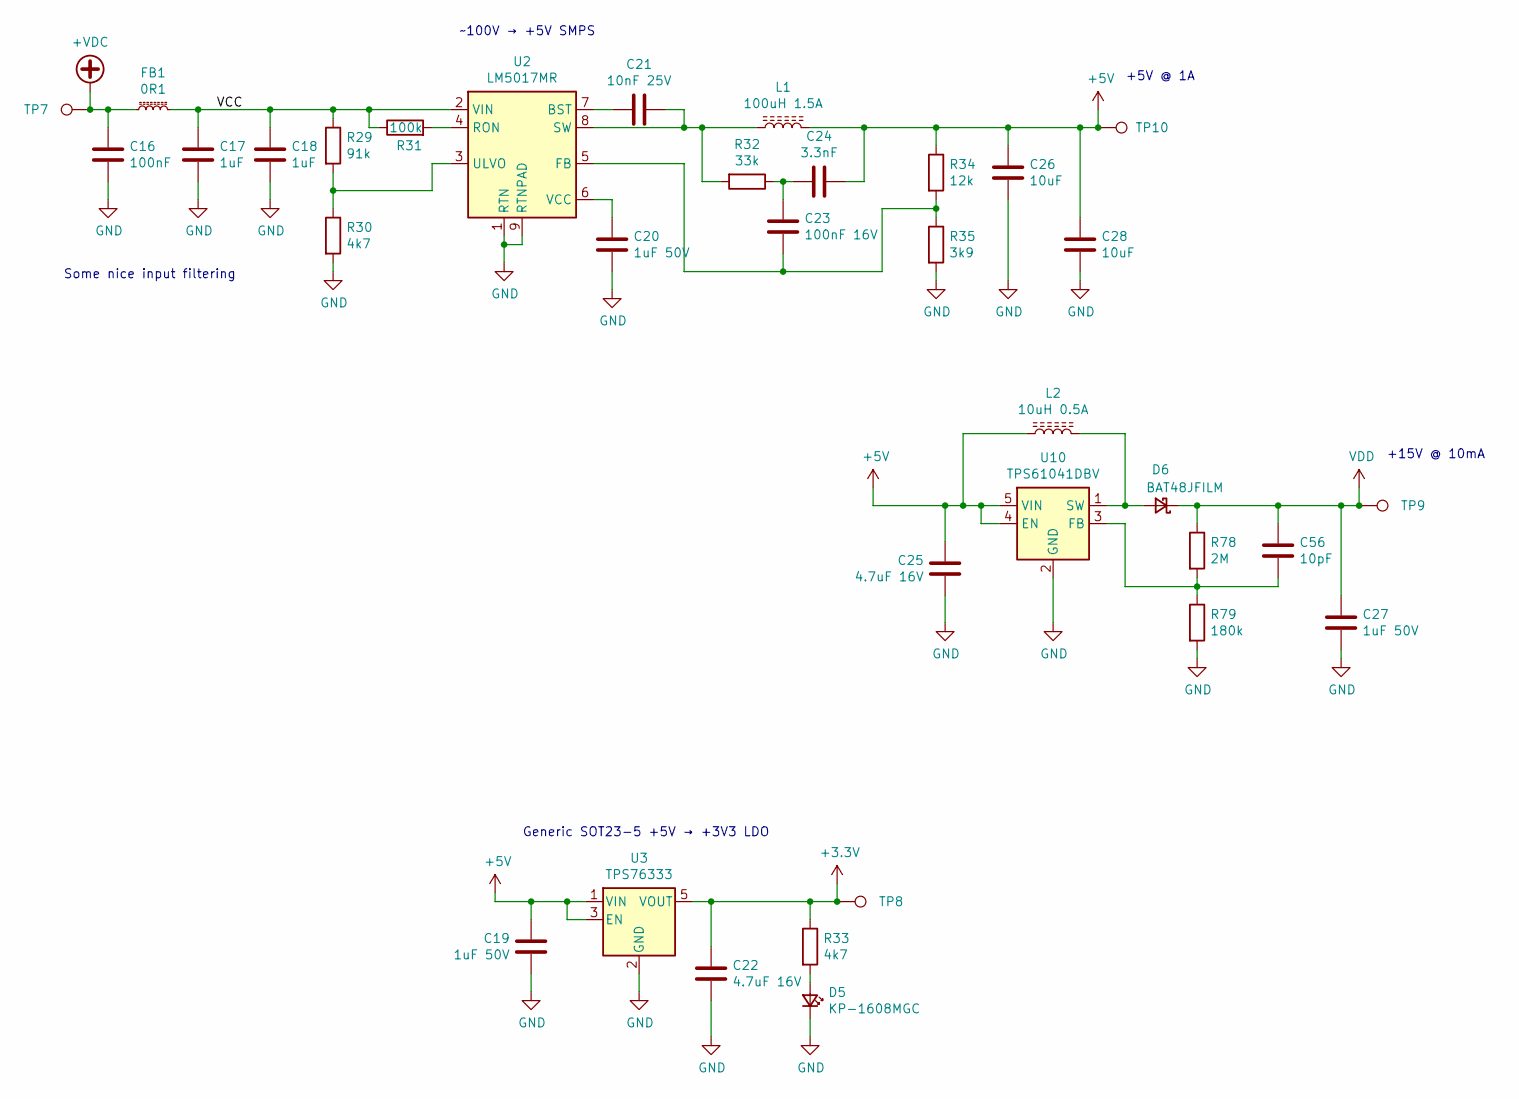
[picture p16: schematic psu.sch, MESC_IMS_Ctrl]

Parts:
C16: 100nF; C_0805_2012Metric; LCSC C28233
C17, C18: 1uF; C_1206_3216Metric; LCSC C13832
C19, C20, C27: 1uF 50V; C_0603_1608Metric; LCSC C15849
C21: 10nF 25V; C_0603_1608Metric; LCSC C57112
C22, C25: 4.7uF 16V; C_0603_1608Metric; LCSC C19666
C23: 100nF 16V; C_0402_1005Metric; LCSC C1525
C24: 3.3nF; C_0402_1005Metric; LCSC C26404
C26, C28: 10uF; C_1206_3216Metric; LCSC C13585
C56: 10pF; C_0402_1005Metric; LCSC C32949
D5: KP-1608MGC; D_0603_1608Metric; LCSC C192316
D6: BAT48JFILM; D_SOD-323; LCSC C109204
FB1: 0R1; L_0603_1608Metric; LCSC C80165
L1: 100uH 1.5A; L_Wuerth_HCI-1040; LCSC C497890
L2: 10uH 0.5A; L_0805_2012Metric; LCSC C281113
R29: 91k; R_0603_1608Metric; LCSC C23265
R30: 4k7; R_0603_1608Metric; LCSC C23162
R31: 100k; R_0603_1608Metric; LCSC C25803
R32: 33k; R_0402_1005Metric; LCSC C25779
R33: 4k7; R_0402_1005Metric; LCSC C25900
R34: 12k; R_0402_1005Metric; LCSC C25752
R35: 3k9; R_0402_1005Metric; LCSC C51721
R78: 2M; R_0402_1005Metric; LCSC C11512
R79: 180k; R_0402_1005Metric; LCSC C25760
TP7, TP8, TP9, TP10: TestPoint; TestPoint_Pad_D1.0mm
U2: LM5017MR; SOIC-8-1EP_3.9x4.9mm_P1.27mm_EP2.41x3.3mm; LCSC C34355
U3: TPS76333; SOT-23-5; LCSC C296219
U10: TPS61041DBV; SOT-23-5; LCSC C9846

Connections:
+5V: C19.1, C24.1, C25.1, C26.1, C28.1, L1.2, L2.1, R34.1, TP10.1, U3.1 (VIN), U3.3 (EN), U10.4 (EN), U10.5 (VIN); also elsewhere on the board
+VDC: C16.1, FB1.1, TP7.1; also elsewhere on the board
/PSUs/VCC: C17.1, C18.1, FB1.2, R29.1, R31.1, U2.2 (VIN)
GND: C16.2, C17.2, C18.2, C19.2, C20.2, C22.2, C25.2, C26.2, C27.2, C28.2, D5.1 (K), R30.2, R35.2, R79.2, U2.1 (RTN), U2.9 (RTNPAD), U3.2 (GND), U10.2 (GND); also elsewhere on the board
unnamed: C20.1, U2.6 (VCC)
unnamed: C21.1, L1.1, R32.2, U2.8 (SW)
unnamed: C21.2, U2.7 (BST)
unnamed: C23.1, C24.2, R32.1
unnamed: C23.2, R34.2, R35.1, U2.5 (FB)
unnamed: C56.2, R78.2, R79.1, U10.3 (FB)
unnamed: D5.2 (A), R33.2
unnamed: D6.2 (A), L2.2, U10.1 (SW)
unnamed: R29.2, R30.1, U2.3 (ULVO)
unnamed: R31.2, U2.4 (RON)
VDD: C27.1, C56.1, D6.1 (K), R78.1, TP9.1; also elsewhere on the board

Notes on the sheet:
Generic SOT23-5 +5V → +3V3 LDO
~~100V → +5V SMPS
Some nice input filtering
+15V @ 10mA
+5V @ 1A

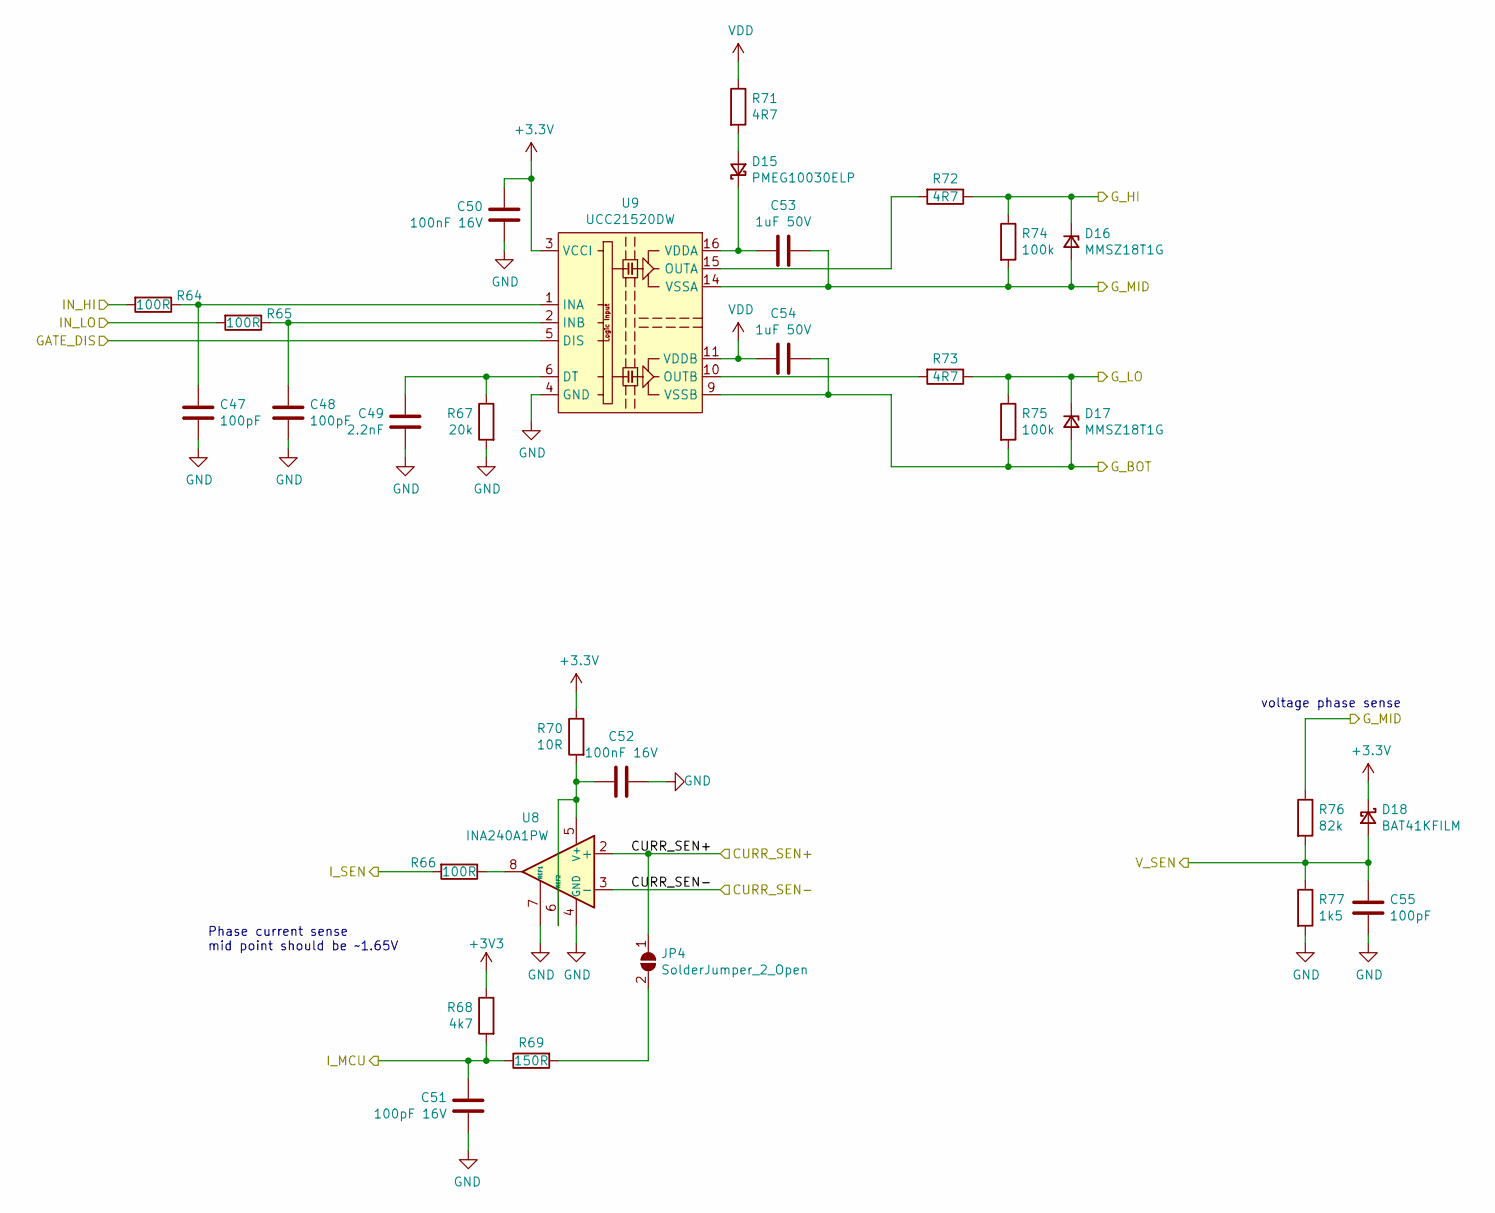
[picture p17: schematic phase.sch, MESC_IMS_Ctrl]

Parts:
C29, C30, C37: 100pF; C_0402_1005Metric; LCSC C1546
C31: 2.2nF; C_0603_1608Metric; LCSC C1604
C32, C34: 100nF 16V; C_0402_1005Metric; LCSC C1525
C33: 100pF 16V; C_0402_1005Metric; LCSC C1546
C35, C36: 1uF 50V; C_0603_1608Metric; LCSC C15849
D7: PMEG10030ELP; D_SOD-128; LCSC C503376
D8, D9: MMSZ18T1G; D_SOD-123; LCSC C382948
D10: BAT41KFILM; D_SOD-523; LCSC C73150
JP2: SolderJumper_2_Open; SolderJumper-2_P1.3mm_Open_RoundedPad1.0x1.5mm
R36, R37, R38: 100R; R_0402_1005Metric; LCSC C25076
R39: 20k; R_0603_1608Metric; LCSC C4184
R40: 4k7; R_0402_1005Metric; LCSC C25900
R41: 150R; R_0402_1005Metric; LCSC C25082
R42: 10R; R_0402_1005Metric; LCSC C25077
R43, R44, R45: 4R7; R_0805_2012Metric; LCSC C17675
R46, R47: 100k; R_0402_1005Metric; LCSC C25741
R48: 82k; R_0603_1608Metric; LCSC C23254
R49: 1k5; R_0603_1608Metric; LCSC C22843
U4: INA240A1PW; TSSOP-8_4.4x3mm_P0.65mm; LCSC C129949
U5: UCC21520DW; SOIC-16W_7.5x10.3mm_P1.27mm; LCSC C189707

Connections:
/ISU_MCU: C33.1, R40.2, R41.1; also elsewhere on the board
/Phase_U/CURR_SEN+: JP2.1 (A), U4.2 (+); also elsewhere on the board
/Phase_U/CURR_SEN-: U4.3 (-); also elsewhere on the board
/Phase_U/GATE_DIS: U5.5 (DIS); also elsewhere on the board
/Phase_U/G_BOT: C36.1, D9.2 (A), R47.2, U5.9 (VSSB); also elsewhere on the board
/Phase_U/G_HI: D8.1 (K), R44.1, R46.1; also elsewhere on the board
/Phase_U/G_LO: D9.1 (K), R45.1, R47.1; also elsewhere on the board
/Phase_U/G_MID: C35.1, D8.2 (A), R46.2, R48.1, U5.14 (VSSA); also elsewhere on the board
/U_IN_HI: R36.2; also elsewhere on the board
/U_IN_LO: R37.2; also elsewhere on the board
/U_I_SEN: R38.2; also elsewhere on the board
/U_V_SEN: C37.1, D10.2 (A), R48.2, R49.1; also elsewhere on the board
GND: C29.2, C30.2, C31.1, C32.2, C33.2, C34.1, C37.2, R39.2, R49.2, U4.1 (GND), U4.4 (GND), U4.7 (REF1), U5.4 (GND); also elsewhere on the board
unnamed: C29.1, R36.1, U5.1 (INA)
unnamed: C30.1, R37.1, U5.2 (INB)
unnamed: C31.2, R39.1, U5.6 (DT)
unnamed: C34.2, R42.2, U4.5 (V+), U4.6 (REF2)
unnamed: C35.2, D7.1 (K), U5.16 (VDDA)
unnamed: D7.2 (A), R43.2
unnamed: JP2.2 (B), R41.2
unnamed: R38.1, U4.8
unnamed: R44.2, U5.15 (OUTA)
unnamed: R45.2, U5.10 (OUTB)
VDD: C36.2, R43.1, U5.11 (VDDB); also elsewhere on the board

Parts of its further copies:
C38, C39, C46, C47, C48, C55: 100pF; C_0402_1005Metric; LCSC C1546
C40, C49: 2.2nF; C_0603_1608Metric; LCSC C1604
C41, C43, C50, C52: 100nF 16V; C_0402_1005Metric; LCSC C1525
C42, C51: 100pF 16V; C_0402_1005Metric; LCSC C1546
C44, C45, C53, C54: 1uF 50V; C_0603_1608Metric; LCSC C15849
D11, D15: PMEG10030ELP; D_SOD-128; LCSC C503376
D12, D13, D16, D17: MMSZ18T1G; D_SOD-123; LCSC C382948
D14, D18: BAT41KFILM; D_SOD-523; LCSC C73150
JP3, JP4: SolderJumper_2_Open; SolderJumper-2_P1.3mm_Open_RoundedPad1.0x1.5mm
R50, R51, R52, R64, R65, R66: 100R; R_0402_1005Metric; LCSC C25076
R53, R67: 20k; R_0603_1608Metric; LCSC C4184
R54, R68: 4k7; R_0402_1005Metric; LCSC C25900
R55, R69: 150R; R_0402_1005Metric; LCSC C25082
R56, R70: 10R; R_0402_1005Metric; LCSC C25077
R57, R58, R59, R71, R72, R73: 4R7; R_0805_2012Metric; LCSC C17675
R60, R61, R74, R75: 100k; R_0402_1005Metric; LCSC C25741
R62, R76: 82k; R_0603_1608Metric; LCSC C23254
R63, R77: 1k5; R_0603_1608Metric; LCSC C22843
U6, U8: INA240A1PW; TSSOP-8_4.4x3mm_P0.65mm; LCSC C129949
U7, U9: UCC21520DW; SOIC-16W_7.5x10.3mm_P1.27mm; LCSC C189707

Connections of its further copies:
/ISV_MCU: C42.1, R54.2, R55.1; also elsewhere on the board
/ISW_MCU: C51.1, R68.2, R69.1; also elsewhere on the board
/Phase_U/GATE_DIS: U7.5 (DIS), U9.5 (DIS); also elsewhere on the board
/Phase_V/CURR_SEN+: JP3.1 (A), U6.2 (+); also elsewhere on the board
/Phase_V/CURR_SEN-: U6.3 (-); also elsewhere on the board
/Phase_V/G_BOT: C45.1, D13.2 (A), R61.2, U7.9 (VSSB); also elsewhere on the board
/Phase_V/G_HI: D12.1 (K), R58.1, R60.1; also elsewhere on the board
/Phase_V/G_LO: D13.1 (K), R59.1, R61.1; also elsewhere on the board
/Phase_V/G_MID: C44.1, D12.2 (A), R60.2, R62.1, U7.14 (VSSA); also elsewhere on the board
/Phase_W/CURR_SEN+: JP4.1 (A), U8.2 (+); also elsewhere on the board
/Phase_W/CURR_SEN-: U8.3 (-); also elsewhere on the board
/Phase_W/G_BOT: C54.1, D17.2 (A), R75.2, U9.9 (VSSB); also elsewhere on the board
/Phase_W/G_HI: D16.1 (K), R72.1, R74.1; also elsewhere on the board
/Phase_W/G_LO: D17.1 (K), R73.1, R75.1; also elsewhere on the board
/Phase_W/G_MID: C53.1, D16.2 (A), R74.2, R76.1, U9.14 (VSSA); also elsewhere on the board
/V_IN_HI: R50.2; also elsewhere on the board
/V_IN_LO: R51.2; also elsewhere on the board
/V_I_SEN: R52.2; also elsewhere on the board
/V_V_SEN: C46.1, D14.2 (A), R62.2, R63.1; also elsewhere on the board
/W_IN_HI: R64.2; also elsewhere on the board
/W_IN_LO: R65.2; also elsewhere on the board
/W_I_SEN: R66.2; also elsewhere on the board
/W_V_SEN: C55.1, D18.2 (A), R76.2, R77.1; also elsewhere on the board
GND: C38.2, C39.2, C40.1, C41.2, C42.2, C43.1, C46.2, C47.2, C48.2, C49.1, C50.2, C51.2, C52.1, C55.2, R53.2, R63.2, R67.2, R77.2, U6.1 (GND), U6.4 (GND), U6.7 (REF1), U7.4 (GND), U8.1 (GND), U8.4 (GND), U8.7 (REF1), U9.4 (GND); also elsewhere on the board
unnamed: C38.1, R50.1, U7.1 (INA)
unnamed: C39.1, R51.1, U7.2 (INB)
unnamed: C40.2, R53.1, U7.6 (DT)
unnamed: C43.2, R56.2, U6.5 (V+), U6.6 (REF2)
unnamed: C44.2, D11.1 (K), U7.16 (VDDA)
unnamed: C47.1, R64.1, U9.1 (INA)
unnamed: C48.1, R65.1, U9.2 (INB)
unnamed: C49.2, R67.1, U9.6 (DT)
unnamed: C52.2, R70.2, U8.5 (V+), U8.6 (REF2)
unnamed: C53.2, D15.1 (K), U9.16 (VDDA)
unnamed: D11.2 (A), R57.2
unnamed: D15.2 (A), R71.2
unnamed: JP3.2 (B), R55.2
unnamed: JP4.2 (B), R69.2
unnamed: R52.1, U6.8
unnamed: R58.2, U7.15 (OUTA)
unnamed: R59.2, U7.10 (OUTB)
unnamed: R66.1, U8.8
unnamed: R72.2, U9.15 (OUTA)
unnamed: R73.2, U9.10 (OUTB)
VDD: C45.2, C54.2, R57.1, R71.1, U7.11 (VDDB), U9.11 (VDDB); also elsewhere on the board

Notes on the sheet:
Phase current sense mid point should be ~~1.65V
voltage phase sense

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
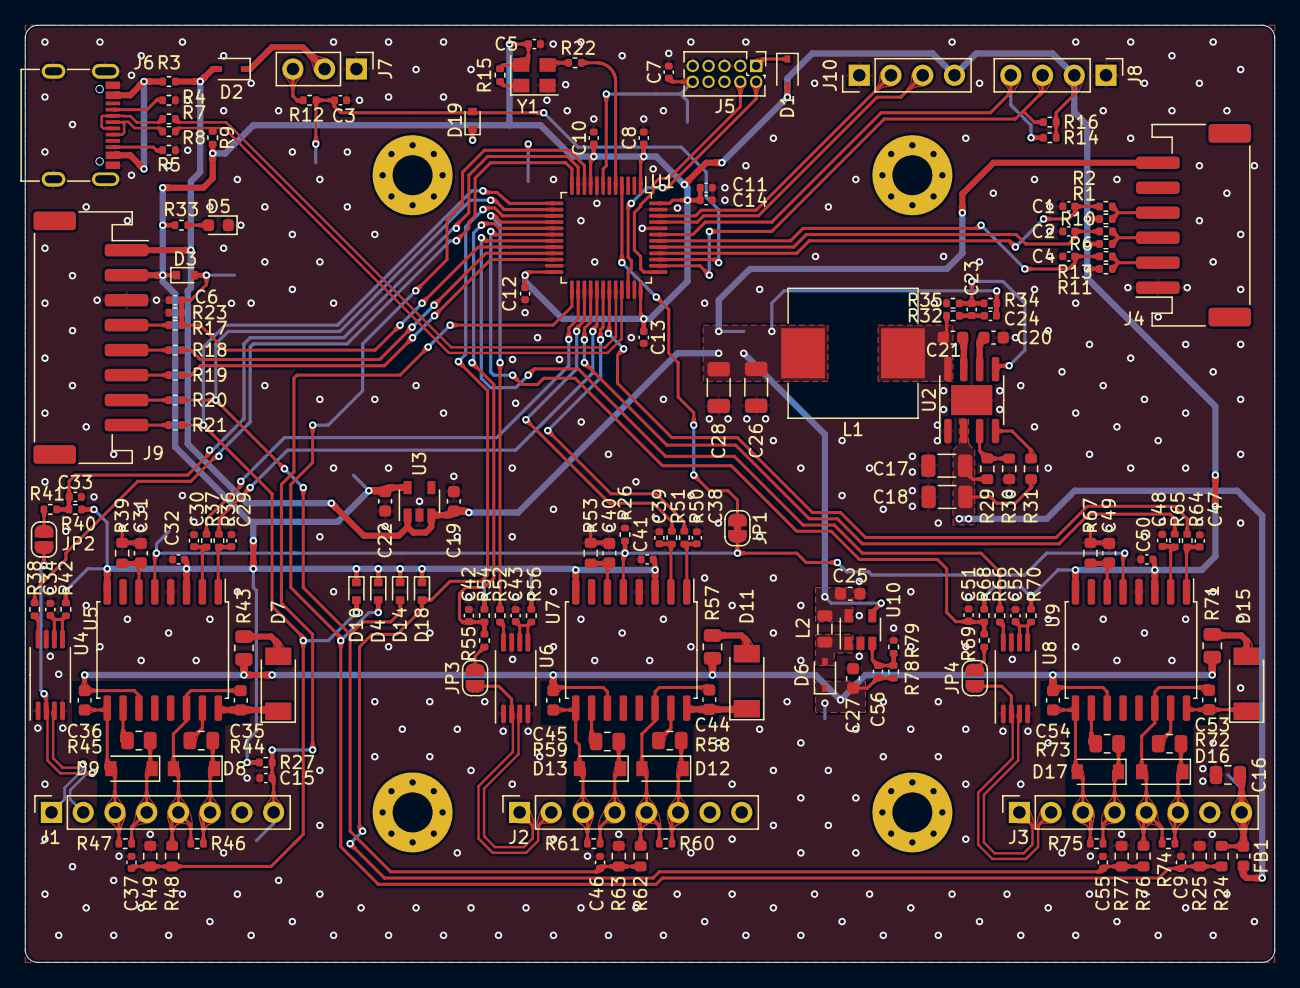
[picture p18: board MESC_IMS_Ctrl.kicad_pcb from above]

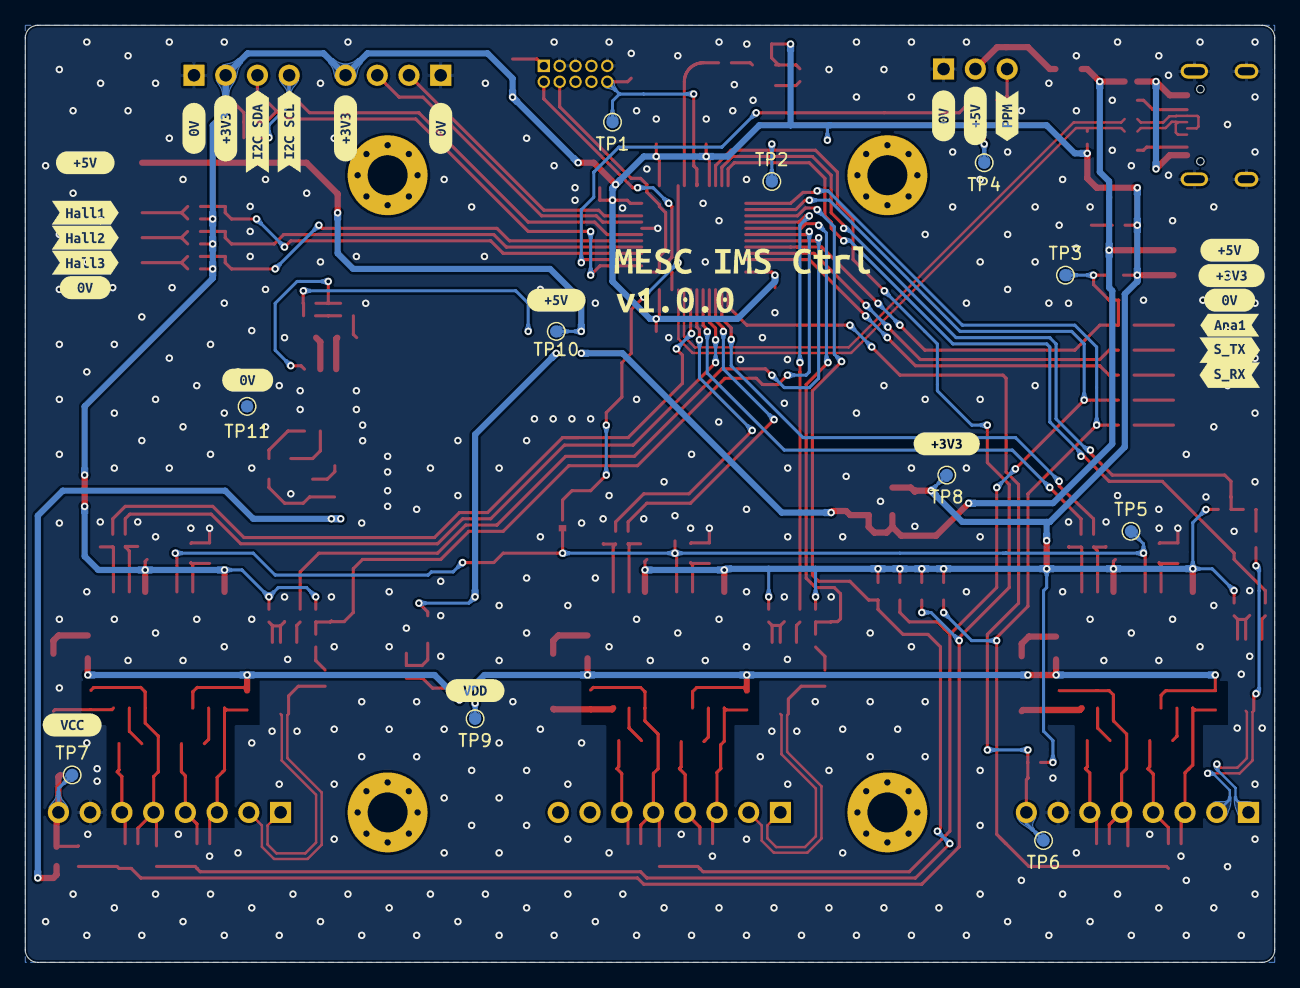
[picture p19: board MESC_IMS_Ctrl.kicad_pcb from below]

Board: 4 copper layers, 100.0 x 75.0 mm, 223 parts (38 on the bottom side), 118 nets.

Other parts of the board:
svg2mod, svg2mod#2, svg2mod#3, svg2mod#4, svg2mod#5, svg2mod#6, svg2mod#7, svg2mod#8, svg2mod#9, svg2mod#10, svg2mod#11, svg2mod#12, svg2mod#13, svg2mod#14, svg2mod#15, svg2mod#16, svg2mod#17, svg2mod#18, svg2mod#19, svg2mod#20, svg2mod#21, svg2mod#22, svg2mod#23: G***; label
svgemod: G***; label
svgemod#2, svgemod#3, svgemod#4: G***; label

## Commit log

2021-04-10 Adding the initial files
    [MESC_IMS_ESC.kicad_pcb, MESC_IMS_ESC.sch, phase.sch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]
2021-04-10 Minor updates
    Tweaking the README.md
    Removing F303 op-amp circuitry.
    Re-arranging INA240 circuit
    [MESC_IMS_ESC.sch, phase.sch]
2021-04-10 Adding some test points
    [MESC_IMS_ESC.sch, phase.sch, psu.sch]
2021-04-11 Assigned all footprints
    Began initial placement
    [MESC_IMS_ESC.kicad_pcb, MESC_IMS_ESC.sch, phase.sch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]
2021-04-11 Minor name change
    [MESC_IMS_Ctrl.kicad_pcb, MESC_IMS_Ctrl.sch, phase.sch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]
2021-04-11 Adding low-side current comparators
    [MESC_IMS_Ctrl.kicad_pcb, MESC_IMS_Ctrl.sch]
2021-04-12 Adding LCSC part numbers
    [MESC_IMS_Ctrl.kicad_pcb, MESC_IMS_Ctrl.sch, phase.sch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]
2021-04-19 Twaeking the layout to fit into 100x100mm
    [MESC_IMS_Ctrl.kicad_pcb, MESC_IMS_Ctrl.sch, phase.sch]
2021-04-19 More placement
    [MESC_IMS_Ctrl.kicad_pcb, MESC_IMS_Ctrl.sch, phase.sch]
2021-04-19 Adding some basic test tracks
    [MESC_IMS_Ctrl.kicad_pcb, MESC_IMS_Ctrl.sch, phase.sch]
2021-04-19 Cleaned up the schematic
    Also regenerated the pdf & set boot diodes to SOD128.
    [MESC_IMS_Ctrl.kicad_pcb, MESC_IMS_Ctrl.sch, phase.sch]
2021-04-20 Initial gate driver placement/routing
    Also adding images to README
    [MESC_IMS_Ctrl.kicad_pcb, MESC_IMS_Ctrl.sch, phase.sch]
2021-04-25 Continuing routing
    [MESC_IMS_Ctrl.kicad_pcb]
2021-04-25 Some more routing
    [MESC_IMS_Ctrl.kicad_pcb, MESC_IMS_Ctrl.sch]
2021-04-26 moved crystal, made curr sense regular
    [MESC_IMS_Ctrl.kicad_pcb]
2021-04-28 Tweaked LM5017 package
    [MESC_IMS_Ctrl.kicad_pcb, psu.sch]
2021-04-28 Removed coupled inductor
    Added TPS61041DB
    [MESC_IMS_Ctrl.kicad_pcb, MESC_IMS_Ctrl.sch, phase.sch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]
2021-04-29 Playing with pours
    [MESC_IMS_Ctrl.kicad_pcb]
2021-05-01 Some minor tweaks
    [MESC_IMS_Ctrl.kicad_pcb]
2021-05-05 Tweaking potential dividers
    [MESC_IMS_Ctrl.kicad_pcb, MESC_IMS_Ctrl.sch, phase.sch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]
2021-05-06 Routing 3V3 reg
    [MESC_IMS_Ctrl.kicad_pcb]
2021-05-06 More routing
    [MESC_IMS_Ctrl.kicad_pcb]
2021-05-08 Routing nearly complete
    some diodes made smaller
    [MESC_IMS_Ctrl.kicad_pcb, MESC_IMS_Ctrl.sch, phase.sch]
2021-05-08 Adding via stitching and teardrops
    [MESC_IMS_Ctrl.kicad_pcb]
2021-05-09 Updated part numbers
    [MESC_IMS_Ctrl.kicad_pcb, MESC_IMS_Ctrl.sch, phase.sch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]
2021-05-09 Adding 0V TP and labels
    [MESC_IMS_Ctrl.kicad_pcb, MESC_IMS_Ctrl.sch, phase.sch]
2021-05-09 upgrading to 4layer
    [MESC_IMS_Ctrl.kicad_pcb, MESC_IMS_Ctrl.sch, phase.sch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]
